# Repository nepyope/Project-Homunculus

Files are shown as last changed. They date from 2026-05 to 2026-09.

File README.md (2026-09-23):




# Project Homunculus

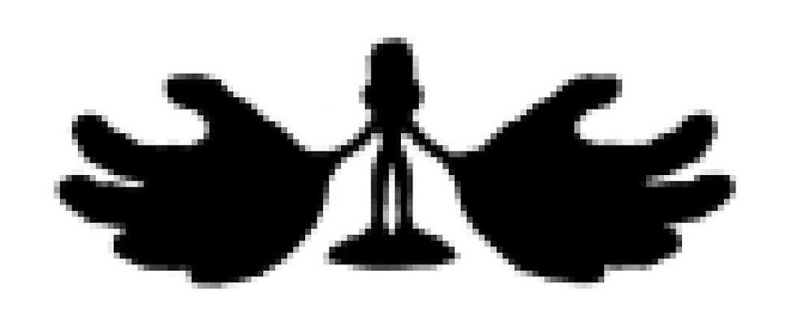
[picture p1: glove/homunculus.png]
Project Homunculus Logo


Project Homunculus is open-source, low-cost hardware for capturing human hand and arm motions. It has two parts. The first is a Hall-effect VR glove that tracks finger joints with magnetic sensors instead of cameras or external tracking stations. The second is a 7-DOF exoskeleton arm for whole-body teleoperation. Together they let you drive dexterous hands and humanoids directly from your own body, so you can collect demonstration data for robot learning without motion-capture rigs or expensive commercial gloves.

The glove is built from off-the-shelf parts (SS49E Hall sensors, an ESP32-C3, a 16-channel multiplexer) and costs under $20 in materials.  Everything is included so you can build, modify, and extend it yourself: firmware, a 3D-printable enclosure, the PCB design, and a Unity visualizer. 

## Repository layout

| Path | Description |
|---|---|
| [`glove/`](glove/) | **Hall Effect VR Glove** — firmware, 3D-printable enclosure, PCB design, Unity hand visualizer, and experimental tools. |
| [`exo/`](exo/) | **Exoskeleton Arm** *(submodule)* — 7-DOF whole-body control device with CAD, firmware, URDF models, and PCB files. |

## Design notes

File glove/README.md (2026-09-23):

  


# Project Homunculus: Hall Effect VR Glove

A hand exoskeleton that reads every finger joint with Hall effect sensors. Each
joint carries a magnet and an SS49E sensor; a custom ESP32-C3 board scans all 16
sensors through a multiplexer and streams the readings over USB serial.

<p align="center">
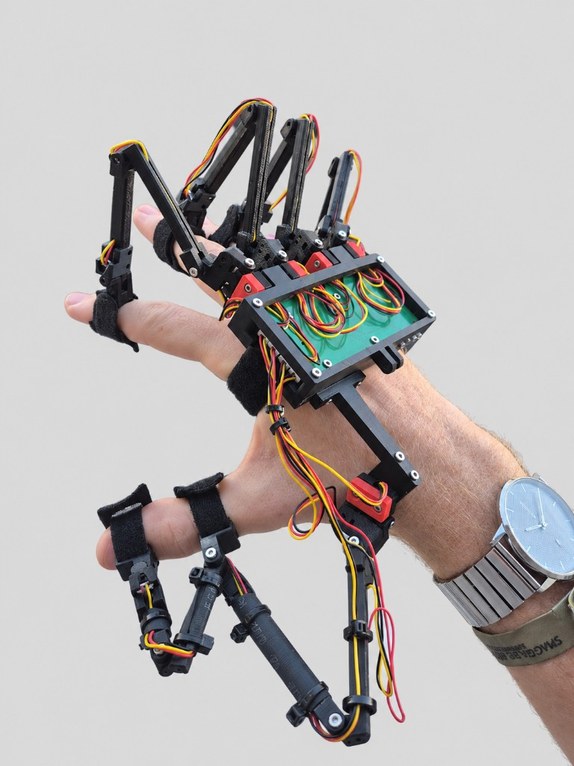
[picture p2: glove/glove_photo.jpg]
The assembled glove worn on a hand
  
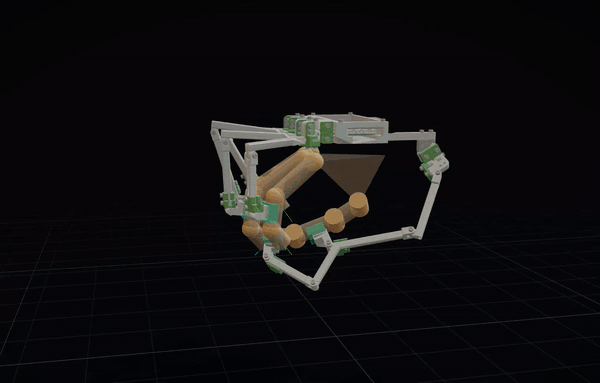
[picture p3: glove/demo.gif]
Glove model articulating in the viewer
  
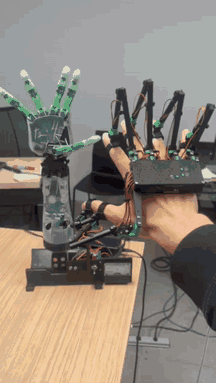
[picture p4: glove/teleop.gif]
Glove teleoperating a robot hand
  
</p>

## Layout

| Path | What |
| --- | --- |
| [`firmware.ino`](firmware.ino) | ESP32-C3 firmware: steps the mux through all 16 channels, reads each sensor on the ADC and prints the values over serial at 115200 baud |
| [`homunculus_pcb/`](homunculus_pcb/) | The sensor board: KiCad project, fab-ready gerbers, BOM and pick-and-place file (see [below](#homunculus_pcb)) |
| [`print/`](print/) | Print plates `left_hand.stl` / `right_hand.stl`: all 47 printed parts per hand, laid flat, about 200 × 204 mm. `make_plates.py` rebuilds them from `model/` |
| [`model/`](model/) | URDF of the glove (`glove_non_diametric.urdf`, 23 revolute DOF) plus the STL meshes it references, in `meshes/printed/` (per joint: MCP, PIP, DIP, palm), `meshes/hardware/` and `meshes/electronics/` |
| [`visualizer/`](visualizer/) | Interactive viewer for `model/` (meshcat 3D view + one slider per joint) and a URDF validator for Onshape re-exports |
| [`BOM.md`](BOM.md) | Bill of materials: boards, power, screws, bearings |
| [`assembly.html`](#assembly) | Interactive 3D assembly guide (see [below](#assembly)) |

## Assembly

**[Open the 3D assembly guide](https://raw.githack.com/nepyope/Project-Homunculus/main/glove/assembly.html)**

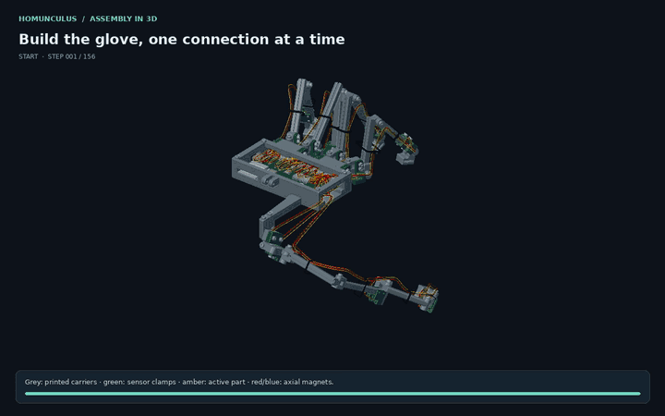
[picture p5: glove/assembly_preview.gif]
Preview of the 3D assembly guide


[`assembly.html`](assembly.html) walks through building the glove step by step in
3D, listing the parts each operation uses. It's a single self-contained file, so
it also works offline: download it and open it in any browser.

### Using the glove with LeRobot

Once assembled and flashed, the glove is supported in LeRobot as the
[`HomunculusGlove`](https://github.com/huggingface/lerobot/blob/main/src/lerobot/teleoperators/homunculus/homunculus_glove.py)
teleoperator. It reads the 16 joint values the firmware streams over serial,
walks you through a per-finger range-of-motion calibration on first connect, and
maps the glove's joints to the HOPE-Jr robot hand.

## homunculus_pcb

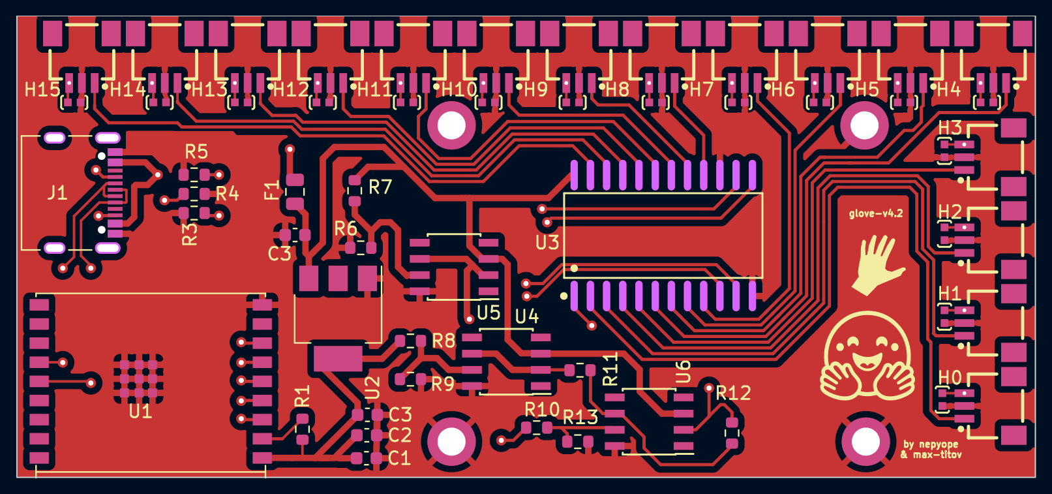
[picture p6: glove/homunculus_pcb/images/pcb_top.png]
PCB top layers


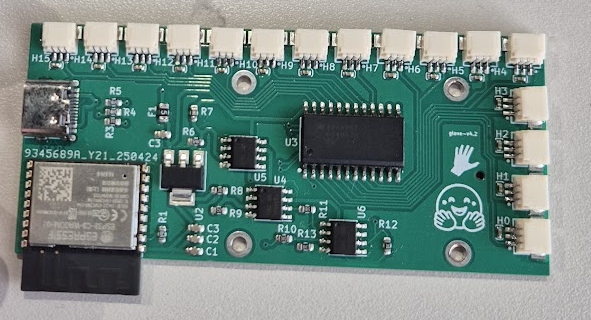
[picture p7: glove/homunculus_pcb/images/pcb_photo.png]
Assembled PCB


An 80 × 36 mm two-layer board (glove-v4.2). Each of the 16 JST SH 3-pin
connectors (`H0`–`H15`) takes one Hall sensor. They feed a CD74HC4067 16-channel
analog mux (`U3`) that the ESP32-C3-WROOM-02 (`U1`) switches and samples. It's
powered from USB-C (`J1`) through a fuse and an AMS1117-3.3 regulator (`U2`), and
three OPA340 op-amps (`U4`–`U6`) sit in the analog path to the ADC.

| Path | What |
| --- | --- |
| [`homunculus_pcb/gerber.zip`](homunculus_pcb/gerber.zip) | Gerbers + drill files, ready to upload to a fab (e.g. JLCPCB) |
| [`homunculus_pcb/BOM.csv`](homunculus_pcb/BOM.csv) | Component list with LCSC part numbers, for PCB assembly |
| [`homunculus_pcb/POS.csv`](homunculus_pcb/POS.csv) | Pick-and-place positions, for PCB assembly |
| [`homunculus_pcb/kicad/pcb/`](homunculus_pcb/kicad/pcb/) | KiCad project: open `desk_display.kicad_pro` (schematic + layout, custom footprints in `lib/`) |
| [`homunculus_pcb/images/`](homunculus_pcb/images/) | The top layer plot from `kicad-cli pcb export svg`, and a photo of the assembled board |

## Acknowledgements

Thank you to everyone who made this glove happen:

- **[Max Titov](https://x.com/maxtitovvv)**, who co-designed the PCB and saw early potential in the glove
- **[Remi Cadene](https://remicadene.com/)**, for bringing the glove to the attention of Hugging Face
- **Hugging Face**, for sponsoring development of the glove for the past year
- **[HOMIE](https://homietele.github.io/)**
- **[Eidon](https://github.com/Eidon-AI/eidon-glove)**
- **The Homunculus community**, on [Discord](https://discord.gg/5bphCGJUGA)

And thanks to everyone else who collaborated on this project: testing, feedback,
ideas and builds all shaped it.

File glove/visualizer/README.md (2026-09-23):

# Glove URDF + viewer

Interactive viewer for the kinematic model of the Project Homunculus sensor
glove (Onshape assembly `glove_non_diametric`), to check that it articulates.
The model itself lives one level up, in [`../model/`](../model/).

```bash
python3 view_glove.py              # 3D view + one slider per joint
python3 view_glove.py --self-test  # no windows: parse, mesh resolution, FK
python3 check_urdf.py ../model/glove_non_diametric.urdf
```

The viewer opens a meshcat render in the browser (`http://127.0.0.1:7000/static/`)
and a slider window, one column per finger. Drag a slider; `F` makes a fist, `R`
zeroes everything, `Q` quits. `--tint` colors each finger chain a flat color
instead of using the export's own materials, which helps when you want to see
which parts belong to which chain. `--no-browser` just prints the URL.

Needs `numpy`, `scipy`, `meshcat` and `pygame`. The viewer is standard-library
plus those four; nothing here imports from LeRobot.

## Layout

| Path | What |
| --- | --- |
| `view_glove.py` | The viewer: URDF parser, forward kinematics, meshcat scene, sliders |
| `check_urdf.py` | Structural validator: link/joint tree, DOF count, mesh existence, optional MuJoCo compile |
| `../model/glove_non_diametric.urdf` | **The working model.** 129 links, 128 joints, 23 revolute DOF |
| `../model/meshes/printed/` | The 3D-printed parts, split per joint like [`../print/individual_stls/`](../print/individual_stls/): `MCP/`, `PIP/`, `DIP/`, `palm/` |
| `../model/meshes/hardware/` | M2 screws and nuts |
| `../model/meshes/electronics/` | PCB, ESP32 module, connectors and passives |
| `onshape/config.json` | onshape-to-robot config — document ID and assembly name, i.e. how to re-export |

Only `view_glove.py` and `../model/` are needed to run the viewer. `check_urdf.py`
is a separate tool and `onshape/config.json` only matters when re-exporting.

## Model

23 DOF across five chains: abduction + MCP + PIP + DIP for each of four fingers,
and a 7-joint thumb. The viewer detects those chains from the kinematic tree
rather than from link names, so it also works on re-exports that get named
differently.

Two things to know about the geometry. The STL vertices are in Onshape
part-studio coordinates, so a part's own frame can sit 25 cm away from its
triangles — don't assume a link origin is anywhere near the mesh you see.
And the export names parts inconsistently within a finger: one chain's links are
`pip_1`, `pip_2`, `_dip_2_1` with no finger name at all, which is why one slider
column is labelled `revolute_4` instead of `pinky`.

## Re-exporting

`onshape/config.json` holds the document ID and assembly name for
onshape-to-robot. If you re-export, run `check_urdf.py` on the result before
anything else — a previous export of this same assembly came out with **0
joints** because the Onshape mates were Fastened rather than Revolute/Slider,
which silently merges every part into one rigid body. Mates must be named
`dof_<name>` for the exporter to emit joints.

Note that mesh filenames are not stable across export runs (they gain and lose
trailing underscores), so a new URDF needs its own mesh folder rather than
reusing `../model/meshes/`.

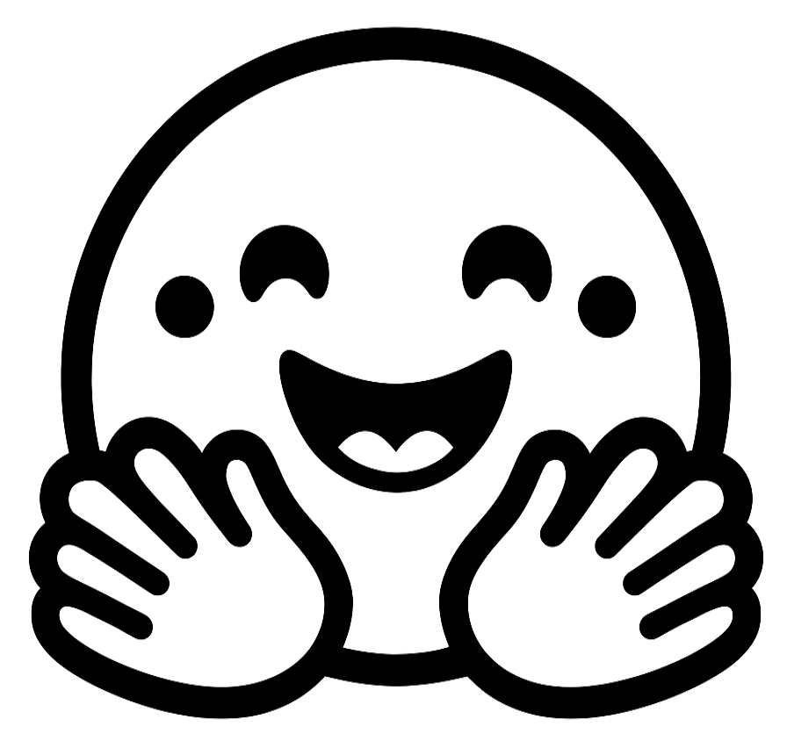
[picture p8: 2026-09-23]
glove/homunculus_pcb/kicad/filtered_image_transparent.png

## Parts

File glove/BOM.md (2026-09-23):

BOM for Homunculus Glove
========================

## Nuts & Bolts 

| M2 | screw set | 1 set | [Amazon](https://amzn.eu/d/cVf2toH) | hand

## Straps & cable management

| Item | Specifications | Quantity | Reference | Details
|-|-|-|-|-
| Velcro finger straps | reusable hook-and-loop ties, 4 in, black | 1 pack of 180 | [Amazon](https://www.amazon.com/dp/B0CJ52WJZY) | hold each finger segment to the exoskeleton
| Cable holders (zip ties) | 100 × 2.5 mm, black | 1 pack of 1000 | [Amazon](https://www.amazon.com/dp/B078NT5F2B) | route the JST cables along the fingers

## PCB
Create an account for [JLCPCB](https://jlcpcb.com/) and place an order for `homunculus_pcb`. Add gerber file and select PCB assembly, in the next screen paste BOM and POS for teleop device and connectors

## Encoders

The PCB's sensor headers are JST **SM03B-SRSS-TB** (SH series, 1.0 mm pitch, 3-pin, side entry). The cables need JST SH 1.0 mm 3-pin plugs (**SHR-03V-S-B** housing, **SSH-003T-P0.2** contacts) on both ends, wired *same direction* (pin 1 to pin 1). Not JST-XH or PH (2.5 / 2.0 mm), those won't fit.

| Item | Specifications | Quantity | Reference | Details
|-|-|-|-|-
| Magnets | neodymium disc, 3 × 2 mm, standard (axially magnetised, not diametric) | 23 | [AliExpress](https://www.aliexpress.com/item/1005001580880407.html) |  1x joint
| SS49E linear hall sensors |  | 28 | [Amazon](https://amzn.eu/d/aemjs7f) | 1x joint (hand + wrist), 2x joint (upper arm)
| JST SH 1.0 mm cables | 3 pins, double-ended, same direction, 28 AWG - length : 10cm | 1 set of 10 | [AliExpress](https://www.aliexpress.com/w/wholesale-JST-SH1.0-3P-double-head-same-direction.html)
| | 3 pins, same direction - length : 15cm | 1 set of 10 | [AliExpress](https://www.aliexpress.com/w/wholesale-JST-SH1.0-3P-double-head-same-direction.html)
| | 3 pins, same direction - length : 20cm | 2 sets of 10 | [AliExpress](https://www.aliexpress.com/w/wholesale-JST-SH1.0-3P-double-head-same-direction.html)
| | 3 pins, same direction - length : 30cm | 1 set of 10 | [AliExpress](https://www.aliexpress.com/w/wholesale-JST-SH1.0-3P-double-head-same-direction.html)

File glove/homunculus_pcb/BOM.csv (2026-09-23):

Designator | Footprint | Quantity | Value | LCSC Part #
C0, C1_13, C1_12, C1_11, C1_10, C1_9, C1_8, C1_7, C1_6, C1_5, C1_3, C1_2, C1, C2, C3_3, C9 | C0402 | 16 | C-0402-0.1uF-16V | C1525
C1_4, C2_2, C3_2, C3 | 0603 | 4 | 10µF
F1 | 0805 | 1 | Fuse_0805_2012Metric
H0, H1, H10, H11, H12, H13, H14, H15, H2, H3, H4, H5, H6, H7, H8, H9 | CONN-SMD_SM03B-SRSS-TB-LF-SN-P | 16 | JST-SM03B | C160403
J1 | USB_C_Receptacle_Palconn_UTC16-G | 1 | USB_C_Receptacle_USB2.0
R1, R4, R5, R6 | 0603 | 4 | 5.11K
R10_2, R10, R11, R12, R8 | 0603 | 5 | 10K
R3 | 0603 | 1 | 1M
R7 | 0603 | 1 | 1K
R9 | 0603 | 1 | 2.4K
U1 | ESP32-C3-WROOM-02 | 1 | ESP32-C3-WROOM-02
U2 | SOT-223-3_TabPin2 | 1 | AMS1117-3.3
U3 | SOIC-24_L15.4-W7.5-P1.27-LS10.3-BL | 1 | CD74HC4067M96 | C496123
U4, U5, U6 | SOIC-8_3.9x4.9mm_Pitch1.27mm | 3 | OPA340UA | C22365307

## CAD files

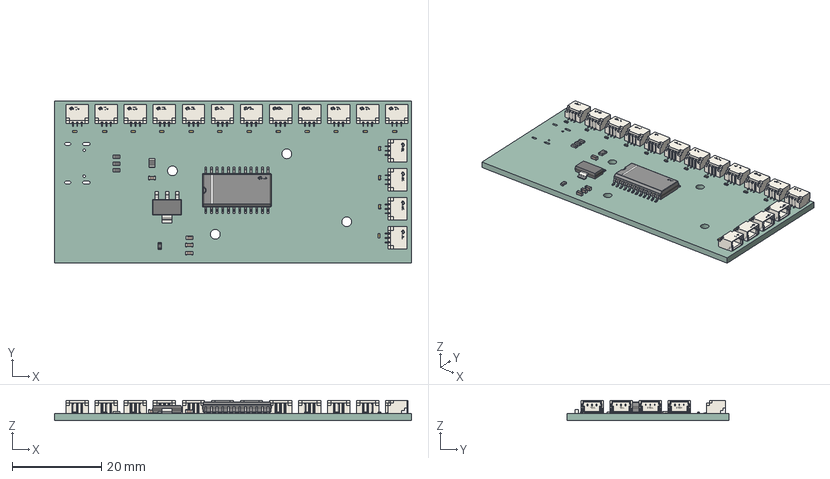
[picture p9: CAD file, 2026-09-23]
glove/homunculus_pcb/kicad/pcb/desk_display.step
79.9 x 36.2 x 4.55 mm
CONN-SMD_SR1.00-WS-3P x 16
R_0603_1608Metric x 4
C0402_L1.0-W0.5-H0.5 x 16
C_0603_1608Metric x 4
SOT_223
SOIC-24_L15.4-W7.5-H2.7-LS10.3-P1.27
Fuse_0805_2012Metric
desk_display_PCB

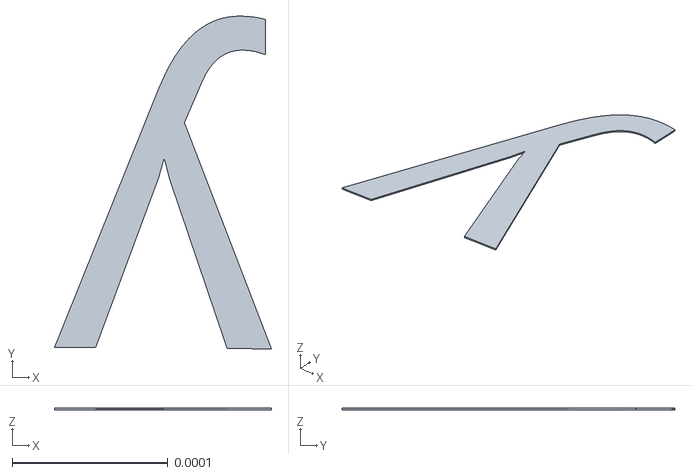
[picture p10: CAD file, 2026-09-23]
glove/model/meshes/electronics/CONN_SMD_SR1_00_WS_3P__1_.stl
0.000139 x 0.000214 x 1e-06

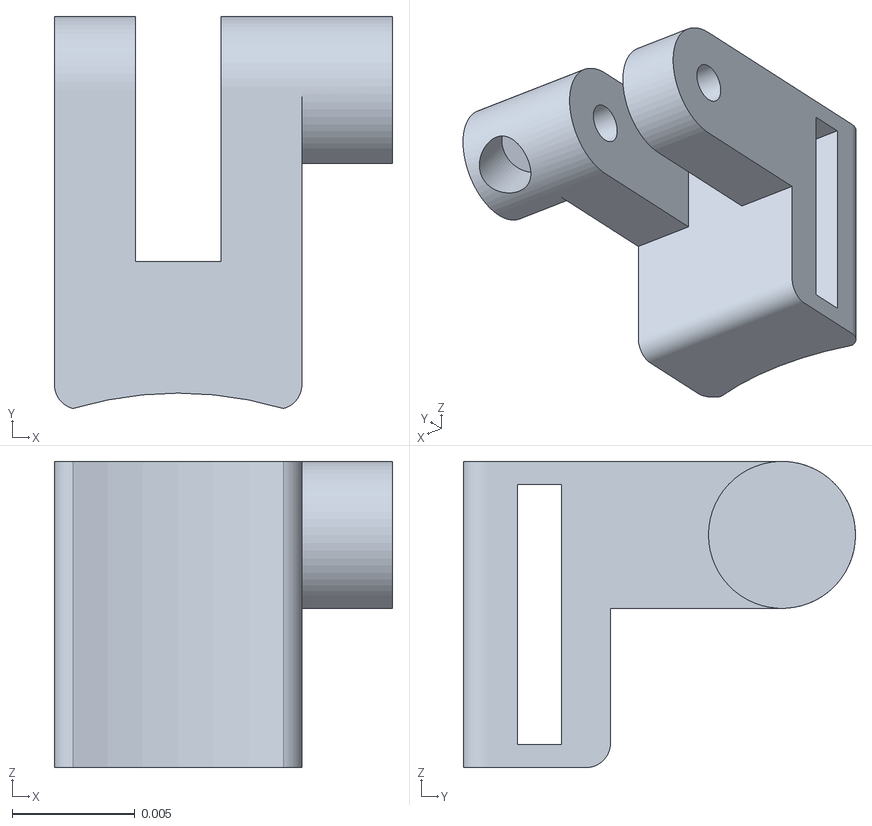
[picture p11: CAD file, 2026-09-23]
glove/model/meshes/printed/DIP/_dip_2.stl
0.0138 x 0.016 x 0.0125

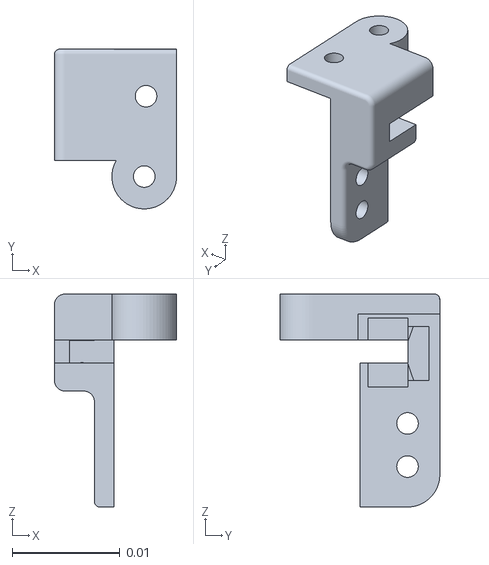
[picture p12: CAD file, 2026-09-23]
glove/model/meshes/printed/MCP/mcp_3_1.stl
0.0113 x 0.0148 x 0.0197

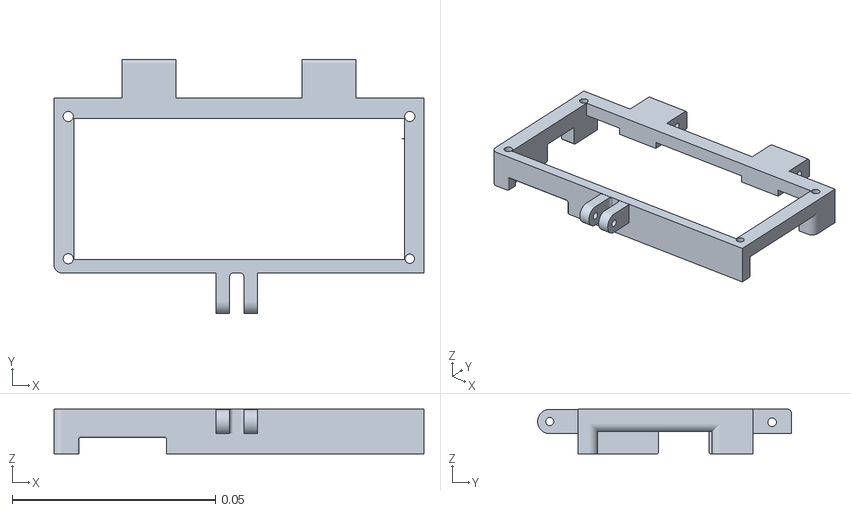
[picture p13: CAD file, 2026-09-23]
glove/model/meshes/printed/palm/top_base.stl
0.091 x 0.0624 x 0.0111

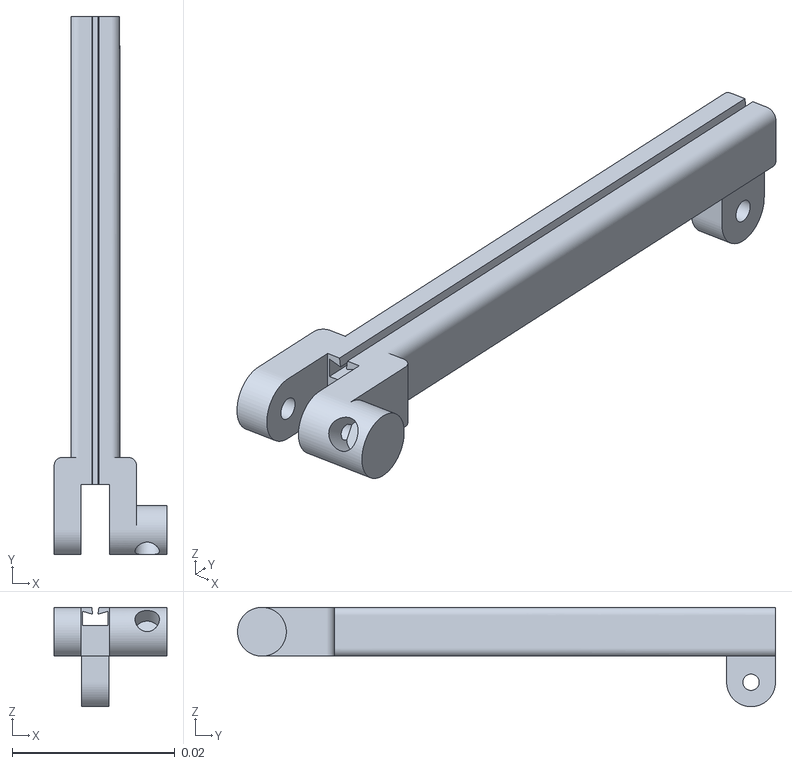
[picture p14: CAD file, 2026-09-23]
glove/model/meshes/printed/PIP/ring_pip_1.stl
0.0138 x 0.0661 x 0.0122

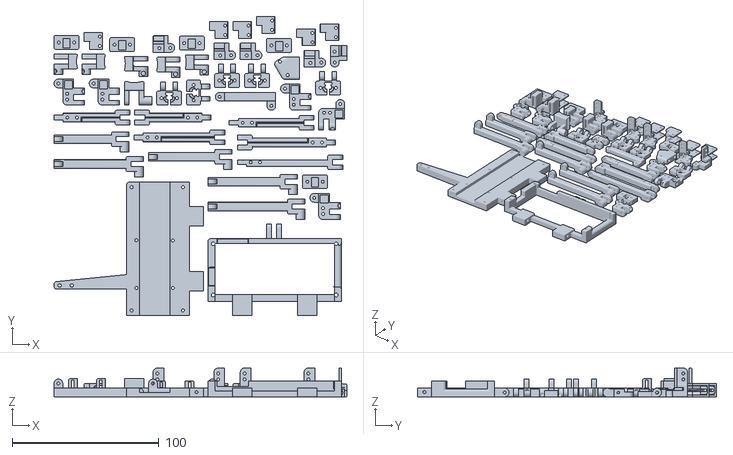
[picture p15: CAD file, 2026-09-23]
glove/print/left_hand.stl
199.8 x 204.0 x 19.8

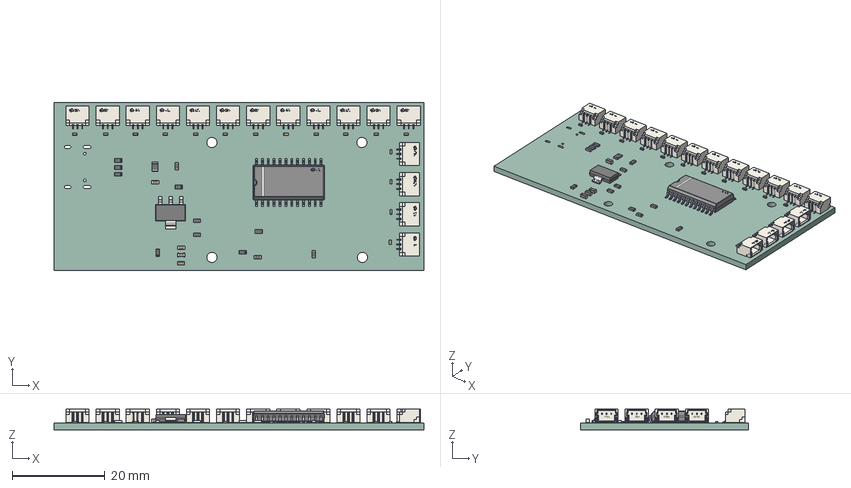
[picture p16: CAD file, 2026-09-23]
glove/homunculus_pcb/kicad/pcb/schee.step
79.9 x 36.2 x 4.50 mm
CONN-SMD_SR1.00-WS-3P x 16
R_0603_1608Metric x 12
C0402_L1.0-W0.5-H0.5 x 16
C_0603_1608Metric x 4
SOT-223
SOIC-24_L15.4-W7.5-H2.7-LS10.3-P1.27
Fuse_0805_2012Metric
desk_display_PCB

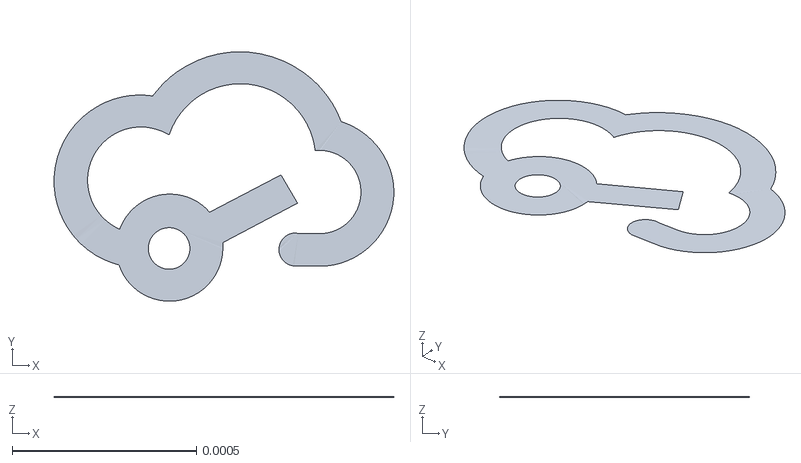
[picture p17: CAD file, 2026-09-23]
glove/model/meshes/electronics/SOIC_24_L15_4_W7_5_H2_7_LS10_3_P1_27__1__7.stl
0.000923 x 0.000677 x 1e-06

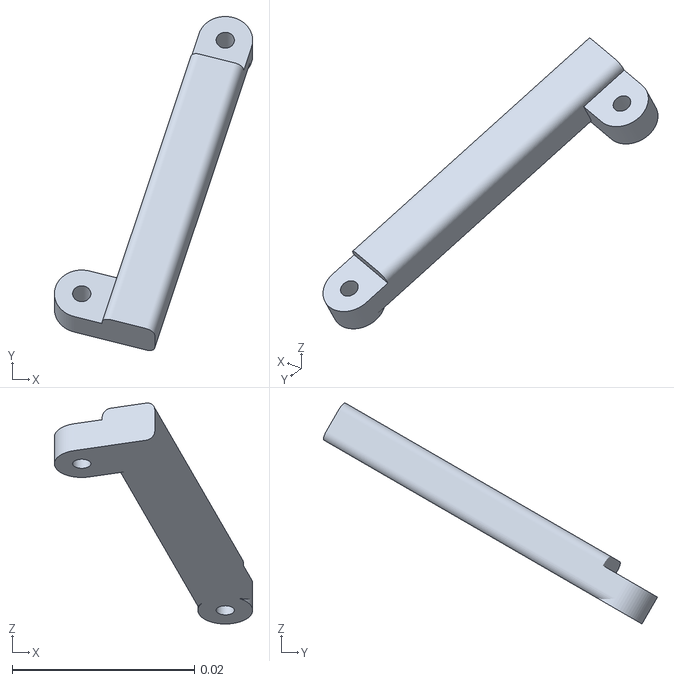
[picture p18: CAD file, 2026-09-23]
glove/model/meshes/printed/DIP/thumb_dip_1.stl
0.0217 x 0.0366 x 0.0242

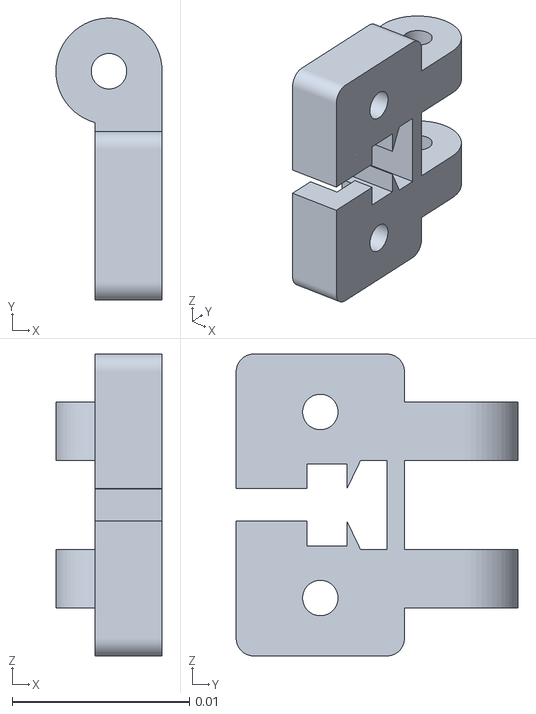
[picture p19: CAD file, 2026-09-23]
glove/model/meshes/printed/MCP/mcp_2.stl
0.006 x 0.0159 x 0.017

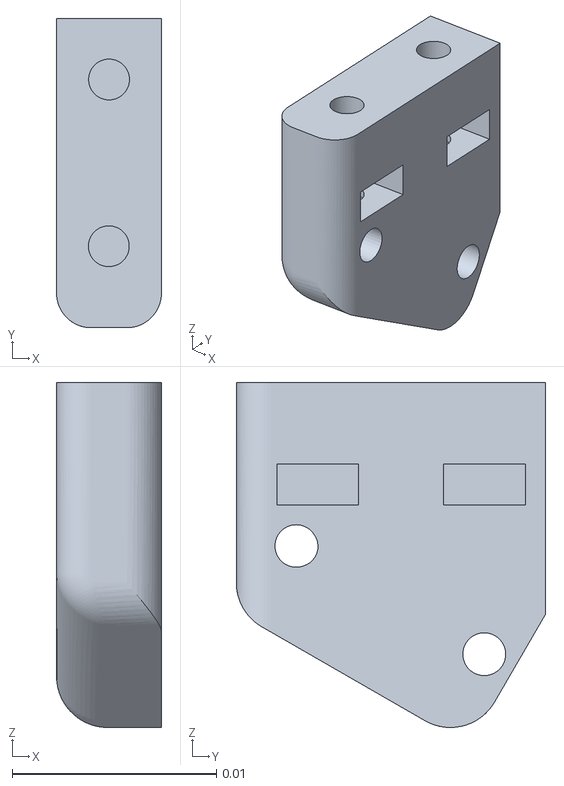
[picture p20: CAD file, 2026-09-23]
glove/model/meshes/printed/palm/thumb_mount.stl
0.00514 x 0.0152 x 0.0169

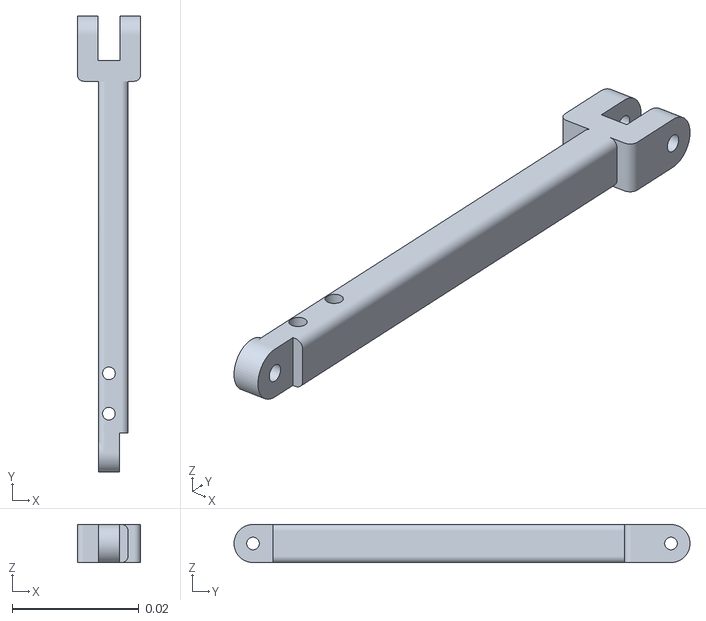
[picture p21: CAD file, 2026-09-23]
glove/model/meshes/printed/PIP/thumb_pip_2.stl
0.01 x 0.072 x 0.006

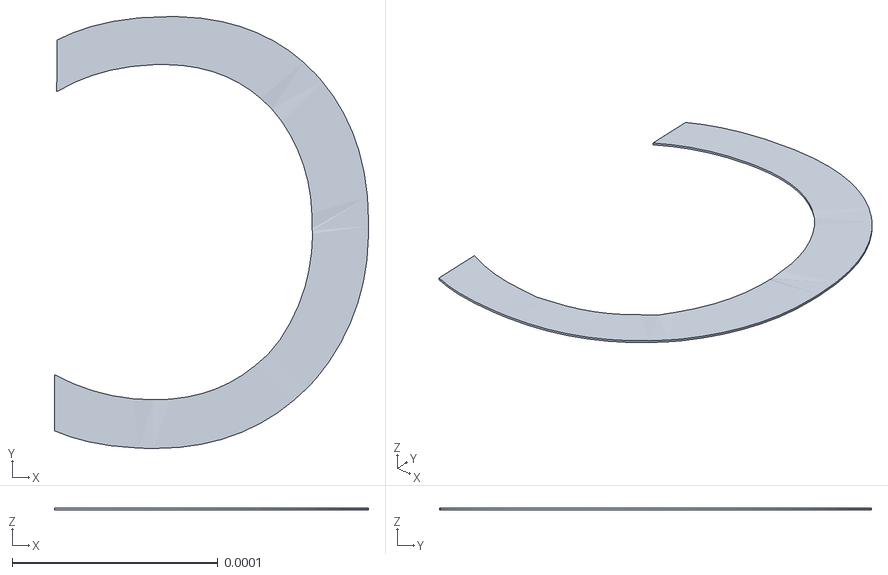
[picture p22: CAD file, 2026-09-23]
glove/model/meshes/electronics/CONN_SMD_SR1_00_WS_3P__1__8.stl
0.000153 x 0.00021 x 1e-06

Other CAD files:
glove/print/right_hand.stl
glove/model/meshes/printed/DIP/thumb_dip_2.stl
glove/model/meshes/printed/MCP/mcp_3.stl
glove/model/meshes/printed/palm/bottom_base.stl
glove/model/meshes/electronics/C0402_L1_0_W0_5_H0_5__1_.stl
glove/model/meshes/electronics/CONN_SMD_SR1_00_WS_3P__1__1.stl
glove/model/meshes/electronics/CONN_SMD_SR1_00_WS_3P__1__10.stl
glove/model/meshes/electronics/CONN_SMD_SR1_00_WS_3P__1__11.stl
glove/model/meshes/electronics/CONN_SMD_SR1_00_WS_3P__1__12.stl
glove/model/meshes/electronics/CONN_SMD_SR1_00_WS_3P__1__13.stl
glove/model/meshes/electronics/CONN_SMD_SR1_00_WS_3P__1__2.stl
glove/model/meshes/electronics/CONN_SMD_SR1_00_WS_3P__1__3.stl
glove/model/meshes/electronics/CONN_SMD_SR1_00_WS_3P__1__4.stl
glove/model/meshes/electronics/CONN_SMD_SR1_00_WS_3P__1__5.stl
glove/model/meshes/electronics/CONN_SMD_SR1_00_WS_3P__1__6.stl
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

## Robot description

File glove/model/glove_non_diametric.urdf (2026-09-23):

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
<robot name="glove_non_diametric">
    <link name="_dip_2">
        <inertial>
            <mass value="9.46839e-07" />
            <origin xyz="-0.00112895 -0.00271042 0.00586256" rpy="-1.40867 1.71032e-05 -1.45331e-05" />
            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
        </inertial>
        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
    </link>
    <link name="_dip_2_1">
        <inertial>
            <mass value="9.46839e-07" />
            <origin xyz="-0.00112895 -0.00294386 0.00574888" rpy="-1.36847 1.69769e-05 -1.38479e-05" />
            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
        </inertial>
        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
    </link>
    <link name="bottom_base">
        <inertial>
            <mass value="2.10374e-05" />
            <origin xyz="-0.0171605 0.0680777 0.00111111" rpy="0 -0 0" />
            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
        </inertial>
        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
    </link>
    <link name="broached_hexagon_socket_head_cap_screw_asme_b18_3_1m___m2x0_4_x_6_steel_grade_2_plain">
        <inertial>
            <mass value="3.80908e-08" />
            <origin xyz="-0.000856737 0 0" rpy="0 -0 0" />
            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
        </inertial>
        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
    </link>
    <link name="broached_hexagon_socket_head_cap_screw_asme_b18_3_1m___m2x0_4_x_6_steel_grade_2_plain__1_">
        <inertial>
            <mass value="3.80908e-08" />
            <origin xyz="-0.000856737 0 0" rpy="0 -0 0" />
            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
        </inertial>
        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
    </link>
    <link name="broached_hexagon_socket_head_cap_screw_asme_b18_3_1m___m2x0_4_x_6_steel_grade_2_plain__2_">
        <inertial>
            <mass value="3.80908e-08" />
            <origin xyz="-0.000856737 -6.93889e-18 0" rpy="0 -0 0" />
            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
        </inertial>
        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
    </link>
    <link name="broached_hexagon_socket_head_cap_screw_asme_b18_3_1m___m2x0_4_x_6_steel_grade_2_plain__3_">
        <inertial>
            <mass value="3.80908e-08" />
            <origin xyz="-0.000856737 6.93889e-18 0" rpy="0 -0 0" />
            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
        </inertial>
        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
    </link>
    <link name="broached_hexagon_socket_head_cap_screw_asme_b18_3_1m___m2x0_4_x_6_steel_grade_2_plain__4_">
        <inertial>
            <mass value="3.80908e-08" />
            <origin xyz="-0.000856737 0 0" rpy="0 -0 0" />
            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
        </inertial>
        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
    </link>
    <link name="broached_hexagon_socket_head_cap_screw_asme_b18_3_1m___m2x0_4_x_6_steel_grade_2_plain__5_">
        <inertial>
            <mass value="3.80908e-08" />
            <origin xyz="-0.000856737 0 0" rpy="0 -0 0" />
            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
        </inertial>
        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
    </link>
    <link name="broached_hexagon_socket_head_cap_screw_asme_b18_3_1m___m2x0_4_x_6_steel_grade_2_plain__6_">
        <inertial>
            <mass value="3.80908e-08" />
            <origin xyz="-0.000856737 0 0" rpy="0 -0 0" />
            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
        </inertial>
        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
    </link>
    <link name="broached_hexagon_socket_head_cap_screw_asme_b18_3_1m___m2x0_4_x_6_steel_grade_2_plain__7_">
        <inertial>
            <mass value="3.80908e-08" />
            <origin xyz="-0.000856737 0 0" rpy="0 -0 0" />
            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
        </inertial>
        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
    </link>
    <link name="broached_hexagon_socket_head_cap_screw_asme_b18_3_1m___m2x0_4_x_6_steel_grade_2_plain__8_">
        <inertial>
            <mass value="3.80908e-08" />
            <origin xyz="0 0.000428713 0.000741757" rpy="0 -0 0" />
            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
        </inertial>
        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
    </link>
    <link name="broached_hexagon_socket_head_cap_screw_asme_b18_3_1m___m2x0_4_x_6_steel_grade_2_plain__9_">
        <inertial>
            <mass value="3.80908e-08" />
            <origin xyz="0 0.000428713 0.000741757" rpy="0 -0 0" />
            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
        </inertial>
        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
    </link>
    <link name="desk_display_pcb__1_">
        <inertial>
            <mass value="4.33853e-06" />
            <origin xyz="-0.0265572 -0.00949047 0.000755" rpy="0 -0 0" />
            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
        </inertial>
        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
    </link>
    <link name="dip_1">
        <inertial>
            <mass value="5.0794e-07" />
            <origin xyz="0.00471641 0.00233039 -0.00309719" rpy="0 -0 0" />
            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
        </inertial>
        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
    </link>
    <link name="dip_1_1">
        <inertial>
            <mass value="5.0794e-07" />
            <origin xyz="0.00470937 -0.00403347 -0.00309719" rpy="0 -0 0" />
            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
        </inertial>
        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
    </link>
    <link name="dip_1_2">
        <inertial>
            <mass value="5.0794e-07" />
            <origin xyz="0.00470937 -0.00403347 0.00310281" rpy="0 -0 0" />
            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
        </inertial>
        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
    </link>
    <link name="dip_1_3">
        <inertial>
            <mass value="5.0794e-07" />
            <origin xyz="0.00471641 0.00233039 0.00310281" rpy="0 -0 0" />
            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
        </inertial>
        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
    </link>
    <link name="dip_1_4">
        <inertial>
            <mass value="5.0794e-07" />
            <origin xyz="0.00471641 0.00233039 -0.00309719" rpy="0 -0 0" />
            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
        </inertial>
        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
    </link>
    <link name="dip_1_5">
        <inertial>
            <mass value="5.0794e-07" />
            <origin xyz="0.00471641 0.00233039 0.00310281" rpy="0 -0 0" />
            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
        </inertial>
        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
    </link>
    <link name="hexagon_socket_head_cap_screw_iso_4762___m2_x_10_steel_4_6_plain">
        <inertial>
            <mass value="4.98905e-08" />
            <origin xyz="-1.99794e-18 -2.22631e-20 -0.00253892" rpy="0 -0 0" />
            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
        </inertial>
        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
    </link>
    <link name="hexagon_socket_head_cap_screw_iso_4762___m2_x_10_steel_4_6_plain__10_">
        <inertial>
            <mass value="4.98905e-08" />
            <origin xyz="-1.99794e-18 -2.22631e-20 -0.00253892" rpy="0 -0 0" />
            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
        </inertial>
        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
    </link>
    <link name="hexagon_socket_head_cap_screw_iso_4762___m2_x_10_steel_4_6_plain__11_">
        <inertial>
            <mass value="4.98905e-08" />
            <origin xyz="-1.98959e-18 -1.11315e-20 -0.00253892" rpy="0 -0 0" />
            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
        </inertial>
        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
    </link>
    <link name="hexagon_socket_head_cap_screw_iso_4762___m2_x_10_steel_4_6_plain__11__1">
        <inertial>
            <mass value="4.98905e-08" />
            <origin xyz="-1.98959e-18 -1.11315e-20 -0.00253892" rpy="0 -0 0" />
            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
        </inertial>
        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
    </link>
    <link name="hexagon_socket_head_cap_screw_iso_4762___m2_x_10_steel_4_6_plain__11__2">
        <inertial>
            <mass value="4.98905e-08" />
            <origin xyz="-1.98959e-18 -1.11315e-20 -0.00253892" rpy="0 -0 0" />
            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
        </inertial>
        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
    </link>
    <link name="hexagon_socket_head_cap_screw_iso_4762___m2_x_10_steel_4_6_plain__11__3">
        <inertial>
            <mass value="4.98905e-08" />
            <origin xyz="-1.98959e-18 -1.11315e-20 -0.00253892" rpy="0 -0 0" />
            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
        </inertial>
        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
    </link>
    <link name="hexagon_socket_head_cap_screw_iso_4762___m2_x_10_steel_4_6_plain__11__4">
        <inertial>
            <mass value="4.98905e-08" />
            <origin xyz="-1.98959e-18 -1.11315e-20 -0.00253892" rpy="0 -0 0" />
            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
        </inertial>
        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
    </link>
    <link name="hexagon_socket_head_cap_screw_iso_4762___m2_x_10_steel_4_6_plain__12_">
        <inertial>
            <mass value="4.98905e-08" />
            <origin xyz="-1.99794e-18 -2.22631e-20 -0.00253892" rpy="0 -0 0" />
            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
        </inertial>
        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
    </link>
    <link name="hexagon_socket_head_cap_screw_iso_4762___m2_x_10_steel_4_6_plain__13_">
        <inertial>
            <mass value="4.98905e-08" />
            <origin xyz="-1.99794e-18 -2.22631e-20 -0.00253892" rpy="0 -0 0" />
            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
        </inertial>
        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
    </link>
    <link name="hexagon_socket_head_cap_screw_iso_4762___m2_x_10_steel_4_6_plain__14_">
        <inertial>
            <mass value="4.98905e-08" />
            <origin xyz="-1.99794e-18 -2.22631e-20 -0.00253892" rpy="0 -0 0" />
            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
        </inertial>
        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
    </link>
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

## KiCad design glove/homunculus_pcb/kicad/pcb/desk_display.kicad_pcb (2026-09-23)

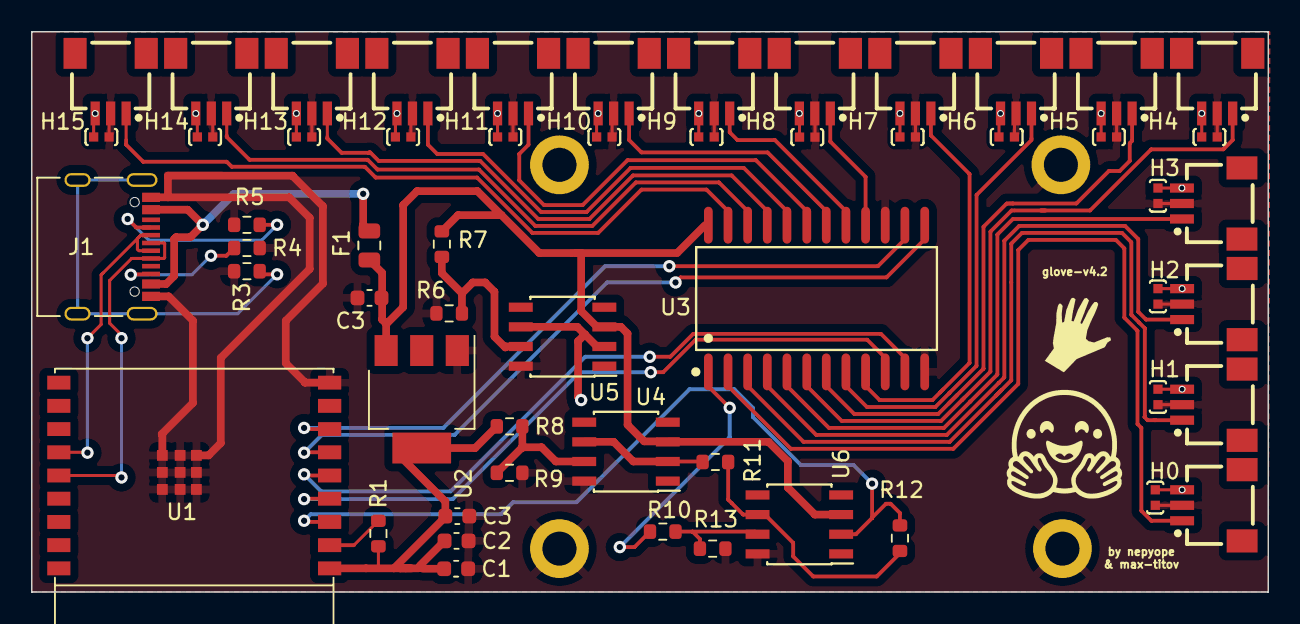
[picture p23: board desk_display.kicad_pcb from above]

Board: 2 copper layers, 79.9 x 36.2 mm, 56 parts (0 on the bottom side), 34 nets.

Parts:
C0, C1, C1#2, C1#3, C1#4, C1#5, C1#6, C1#7, C1#8, C1#9, C1#11, C1#12, C1#13, C2#2, C3, C9: C-0402-0.1uF-16V; C0402
C1#10, C2, C3#2, C3#3: 10µF; C_0603_1608Metric
F1: Fuse_0805_2012Metric
H0, H1, H2, H3, H4, H5, H6, H7, H8, H9, H10, H11, H12, H13, H14, H15: JST-SM03B; CONN-SMD_SM03B-SRSS-TB-LF-SN-P
J1: USB_C_Receptacle_USB2.0; USB_C_Receptacle_Palconn_UTC16-G
R1, R4, R5, R6: 5.11K; R_0603_1608Metric
R3: 1M; R_0603_1608Metric
R7: 1K; R_0603_1608Metric
R8, R10, R10#2, R11, R12: 10K; R_0603_1608Metric
R9: 2.4K; R_0603_1608Metric
U1: ESP32-C3-WROOM-02
U2: AMS1117-3.3; SOT-223-3_TabPin2
U3: CD74HC4067M96; SOIC-24_L15.4-W7.5-P1.27-LS10.3-BL
U4, U5, U6: OPA340UA; SOIC-8_3.9x4.9mm_Pitch1.27mm

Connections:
+0.6V: R8.2, R9.1, R11.1, U4.2, U4.6, U4.7
+3.3V: C1#10.1, C2.1, C3#3.1, R1.1, R8.1, U1.1 (3V3), U2.2 (VO)
+4.2V: C0.2, C1.2, C1#2.2, C1#4.2, C1#5.2, C1#6.2, C1#7.2, C1#8.2, C1#9.2, C1#11.2, C1#12.2, C1#13.2, C2#2.2, C3.2, C9.2, H0.3, H1.3, H2.3, H3.1 (3), H4.3, H5.3, H6.3, H7.3, H8.3, H9.3, H10.3, H11.3, H12.1 (3), H13.3, H14.3, H15.3, R6.1, R7.2, U5.2, U5.6, U5.7
+5VD: C3#2.1, F1.1, F1.2, J1.A4 (VBUS), J1.A9 (VBUS), J1.B4 (VBUS), J1.B9 (VBUS), R7.1, U2.3 (VI), U3.24 (VCC), U4.3, U5.3, U6.3
D+: J1.A6 (D+), J1.B6 (D+), U1.14 (GPIO19/USB_D+)
D-: J1.A7 (D-), J1.B7 (D-), U1.13 (GPIO18/USB_D-)
EN: R1.2, U1.2 (EN/CHIP_PU)
GND: C0.1, C1.1, C1#2.1, C1#3.1, C1#4.1, C1#5.1, C1#6.1, C1#7.1, C1#8.1, C1#9.1, C1#10.2, C1#11.1, C1#12.1, C1#13.1, C2.2, C2#2.1, C3.1, C3#2.2, C3#3.2, C9.1, H0.2, H1.2, H2.2, H3.2, H4.2, H5.2, H6.2, H7.2, H8.2, H9.2, H10.2, H11.2, H12.2, H13.2, H14.2, H15.2, J1.A1 (GND), J1.A12 (GND), J1.B1 (GND), J1.B12 (GND), R3.2, R4.2, R5.2, R6.2, R9.2, R10.2, U1.9 (GND), U1.19 (GND), U2.1 (GND), U3.12 (GND), U3.15 (~E), U4.8, U5.8, U6.8
H*: R11.2, R12.1, R12.2, U1.3 (GPIO4/ADC1_CH4), U6.2, U6.6
HALL_0: H0.1, U3.2 (I7)
HALL_1: H1.1, U3.3 (I6)
HALL_2: H2.1, U3.4 (I5)
HALL_3: H3.1, U3.5 (I4)
HALL_4: H4.1, U3.6 (I3)
HALL_5: H5.1, U3.7 (I2)
HALL_6: H6.1, U3.8 (I1)
HALL_7: H7.1, U3.9 (I0)
HALL_8: H8.1, U3.16 (I15)
HALL_9: H9.1, U3.17 (I14)
HALL_10: H10.1, U3.18 (I13)
HALL_11: H11.1, U3.19 (I12)
HALL_12: H12.1, U3.20 (I11)
HALL_13: H13.1, U3.21 (I10)
HALL_14: H14.1, U3.22 (I9)
HALL_15: H15.1, U3.23 (I8)
MUX_OUT: R10.1, R10#2.1, R10#2.2, U3.1 (COMMONINPUT/OUTPUT), U6.7
NC: U4.1, U4.4, U5.4, U6.1, U6.4
unnamed: J1.A5 (CC1), R5.1
unnamed: J1.B5 (CC2), R4.1
unnamed: J1.S1 (SHIELD), R3.1
S0: U1.4 (GPIO5/ADC2_CH0), U3.10 (S0)
S1: U1.5 (GPIO6), U3.11 (S1)
S2: U1.6 (GPIO7), U3.13 (S3)
S3: U1.7 (GPIO8), U3.14 (S2)

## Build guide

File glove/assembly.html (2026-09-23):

H

HOMUNCULUSAssembly in 3D

Original CAD · all hardware retained

Hall / JST · 5 stepsPCB circuitFull assembly

Loading your actual CAD partsPreparing the assembly…

ASSEMBLY LAB

# Build the glove.

Fit viewOther sideUnderneathSave image

Existing parts Moving part Insertion axis

Drag to orbit · scroll to zoom · click the PCB to explore its circuit

Ready0%

← Previous▶ Play operationNext →Speed Auto-next

CHAPTER

OPERATION

Red · VCCBlack · GNDYellow · signal

CHECK

## Parts in this operation

Show surrounding assembly See through mating parts Show cables and board plugs Show insertion guides

About this reconstruction

Printed parts and hardware use the exact source STL triangles and URDF transforms. Assembly paths follow the mating geometry and your reference. They are an assembly illustration, not a certified collision or tolerance simulation.

Added axial magnets follow the measured blind-pocket axes; N faces outward. The folded Hall bodies, mating JST plugs and 48 wire conductors are new reference-derived geometry. Their dimensions and flexible routes are illustrative. The 16 board sockets are original CAD.

Wire roles follow your confirmed wiring: red VCC, black ground, yellow signal. Each Hall sensing face sits square to its fixed hinge housing. P01–P16 identify physical sockets; their firmware ADC channel order is not established here.

Two thumb covers lack screw instances; those steps are marked. The thumb contact piece and following link share the same M2 × 12 pivot; fit both before inserting that screw.

435 CAD visuals · 70 screws · 10 nuts · 16 magnets · 16 cables / 48 conductors
Underside lead insertion · five stages · sensor faces square to hinges

Close ×

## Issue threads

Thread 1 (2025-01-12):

CAD files?

sisyphean-task, 2025-01-12:
Hi, I love your work on this and the way you presented it in the video. Similarly to Max Titov, I wanted to build this to control a 16-DoF hand, and noticed that you updated the print files, which are now much different than your previous iteration, and seem better to assemble as it does not require gluing the hall effect sensor boxes to the links. After printing, though, I noticed that the thickness of the walls next to the holes was a bit too slim such that the parts accidentally snapped when handling. Do you gave the solid part files to edit these thicknesses, or was this also done in blender making it a bit more difficult (for me, a primarily CAD user) to edit?

nepyope, 2025-01-12:
Thank you for pointing this out, do you have some pics? Anyways yeah its all done in blender lol. it's not too difficult though, there's a .blend file in the print folder which contains the models in obj format, and if you press tab you can move the vertices around. Alternatively you can probably import the obj into freecad and take it from there

sisyphean-task, 2025-01-12:
Ah I see.

I printed the pieces in PLA with a 0.4 mm nozzle which results in the walls no longer being continuous. Here's some pictures of the part and the slicing which creates the issue. I could try slicing using a 0.25 mm nozzle, but regardless it is good practice to have the distance from the center of a hole to an edge be at least the diameter of the hole. I'm not entirely sure if that is the case here?

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

nepyope, 2025-01-13:
Thanks for the help, i'll fix asap

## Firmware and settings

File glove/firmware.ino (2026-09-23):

#include <Arduino.h>

// ─── Multiplexer pins ───────────────────────────────────────────────────
#define S0 5
#define S1 6
#define S2 8
#define S3 7
#define SENSOR_INPUT 4    // analog pin

#define SENSOR_COUNT 16

int rawVals[SENSOR_COUNT];

// scan order through the mux
uint8_t scanOrder[SENSOR_COUNT] = {
  7,6,5,4,3,2,1,0,
  15,14,13,12,11,10,9,8
};

void selectMuxChannel(uint8_t channel) {
  digitalWrite(S0, channel & 0x01);
  digitalWrite(S1, (channel >> 1) & 0x01);
  digitalWrite(S2, (channel >> 2) & 0x01);
  digitalWrite(S3, (channel >> 3) & 0x01);
}

void measureRawValues() {
  for (uint8_t i = 0; i < SENSOR_COUNT; i++) {
    uint8_t ch = scanOrder[i];
    selectMuxChannel(ch);
    delayMicroseconds(100);
    rawVals[i] = analogRead(SENSOR_INPUT);
  }
}

void setup() {
  Serial.begin(115200);
  pinMode(S0, OUTPUT);
  pinMode(S1, OUTPUT);
  pinMode(S2, OUTPUT);
  pinMode(S3, OUTPUT);
  digitalWrite(S0, LOW);
  digitalWrite(S1, LOW);
  digitalWrite(S2, LOW);
  digitalWrite(S3, LOW);
}

void loop() {
  measureRawValues();

  for (uint8_t i = 0; i < SENSOR_COUNT; i++) {
    Serial.print(rawVals[i]);
    Serial.print(' ');
  }

  Serial.println();
  delay(1);
}

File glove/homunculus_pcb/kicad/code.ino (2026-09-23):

#include <Arduino.h>

// Define multiplexer input pins
#define S0 5
#define S1 6
#define S2 7
#define S3 8
#define SENSOR_INPUT 4  // Analog input on GPIO 3

#define SENSOR_COUNT 16

int rawVals[SENSOR_COUNT];

void measureRawValues() {
  for (uint8_t i = 0; i < SENSOR_COUNT; i++) {
    digitalWrite(S0, i & 0b1);
    digitalWrite(S1, i >> 1 & 0b1);
    digitalWrite(S2, i >> 2 & 0b1);
    digitalWrite(S3, i >> 3 & 0b1);
    delay(1);
    
    rawVals[i] = analogRead(SENSOR_INPUT);
  }
}

void printRawValues() {
  for (uint8_t i = 0; i < SENSOR_COUNT; i++) {
    Serial.print(rawVals[i]);
    if (i < SENSOR_COUNT - 1) Serial.print(" ");
  }
  Serial.println();
}

void setup() {
  Serial.begin(115200);
  analogReadResolution(12);

  pinMode(S0, OUTPUT);
  pinMode(S1, OUTPUT);
  pinMode(S2, OUTPUT);
  pinMode(S3, OUTPUT);

  digitalWrite(S0, LOW);
  digitalWrite(S1, LOW);
  digitalWrite(S2, LOW);
  digitalWrite(S3, LOW);
}

void loop() {
  measureRawValues();
  printRawValues();
  delay(10);
}

i can change the range for which im sensing the angle by placing the sensor closer or further away

its literally perfect

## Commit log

2024-09-18 add stls
    [left_hand.stl, right_hand.stl]
2025-02-24 break stl into individual MCP DIP PIP IP
    [dip_1.stl, dip_2.stl, ip_1.stl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]
2025-02-24 add base
    [base.stl, lid.stl, thumb_MCP_holder.stl]
2025-02-24 link to max's pcb
    [base.stl, lid.stl]
2025-02-24 add correct enclosure
    [base.stl, lid.stl]
2025-02-25 use m2 nuts instead of threaded inserts for m2 base (ty robertdalesmith)
    [thumb_MCP_holder.stl]
